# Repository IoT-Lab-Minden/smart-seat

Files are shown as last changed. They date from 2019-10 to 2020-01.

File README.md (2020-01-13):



# SmartSeat

SmartSeat is an office chair that automatically detects and adjusts to the user's favorite seat settings.

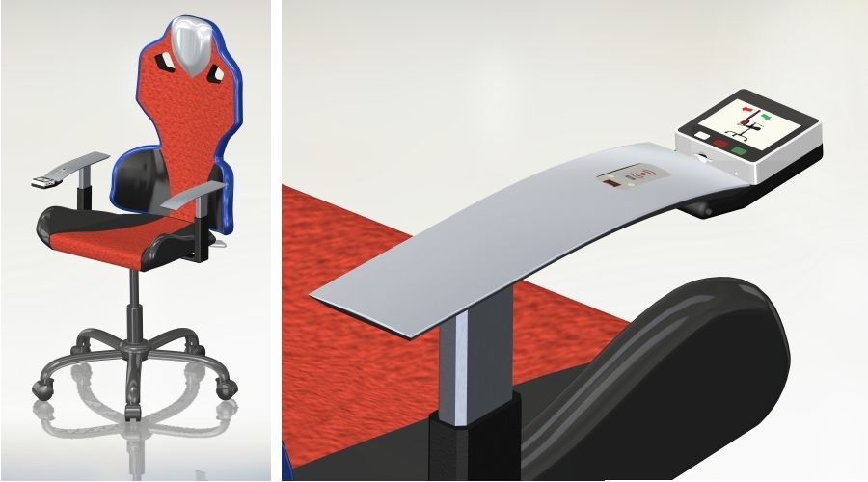
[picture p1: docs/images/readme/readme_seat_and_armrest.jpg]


## For documentation head over to the
## [SmartSeat-Wiki](https://github.com/IoT-Lab-Minden/smart-seat/wiki)

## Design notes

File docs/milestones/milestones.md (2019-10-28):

### 28.10.19: Rohkonstruktion / vorläufige Stückliste

### 04.11.19: jeweils eine Servo Baugruppe mechanisch fertig

### 11.11.19: Servo Baugruppe funktionsfähig

### 18.11.19: RFID lese und schreibfähig

### 09.12.19: Teile gedruckt

### 16.12.19: Aufbau komplett

### 13.01.20: Projektabgabe

### 20.01.20: Projektvorstellung

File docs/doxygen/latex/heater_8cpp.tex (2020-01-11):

\hypertarget{heater_8cpp}{}\doxysection{main/src/heater.cpp File Reference}
\label{heater_8cpp}\index{main/src/heater.cpp@{main/src/heater.cpp}}

Source code for the \mbox{\hyperlink{class_heater}{Heater}} class.  

{\ttfamily \#include \char`\"{}../include/heater.\+hpp\char`\"{}}\newline

\doxysubsection{Detailed Description}
Source code for the \mbox{\hyperlink{class_heater}{Heater}} class. 

\begin{DoxyAuthor}{Author}
Torsten Niemeier 

E-\/mail\+: \href{mailto:tniemeier1@fh-bielefeld.de}{\texttt{ tniemeier1@fh-\/bielefeld.\+de}} 
\end{DoxyAuthor}
\begin{DoxyVersion}{Version}
1.\+0 
\end{DoxyVersion}
\begin{DoxyDate}{Date}
2019/12/21
\end{DoxyDate}
\hypertarget{statemachine_8cpp_LICENSE}{}\doxysubsection{L\+I\+C\+E\+N\+SE}\label{statemachine_8cpp_LICENSE}
This program is free software; you can redistribute it and/or modify it under the terms of the G\+NU General Public License as published by the Free Software Foundation; either version 2 of the License, or (at your option) any later version.

This program is distributed in the hope that it will be useful, but W\+I\+T\+H\+O\+UT A\+NY W\+A\+R\+R\+A\+N\+TY; without even the implied warranty of M\+E\+R\+C\+H\+A\+N\+T\+A\+B\+I\+L\+I\+TY or F\+I\+T\+N\+E\+SS F\+OR A P\+A\+R\+T\+I\+C\+U\+L\+AR P\+U\+R\+P\+O\+SE. See the G\+NU General Public License for more details at \href{https://www.gnu.org/copyleft/gpl.html}{\texttt{ https\+://www.\+gnu.\+org/copyleft/gpl.\+html}}\hypertarget{statemachine_8cpp_DESCRIPTION}{}\doxysubsection{D\+E\+S\+C\+R\+I\+P\+T\+I\+ON}\label{statemachine_8cpp_DESCRIPTION}
The \mbox{\hyperlink{class_heater}{Heater}} class represents a physically present heating element.

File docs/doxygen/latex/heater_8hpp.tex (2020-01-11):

\hypertarget{heater_8hpp}{}\doxysection{main/include/heater.hpp File Reference}
\label{heater_8hpp}\index{main/include/heater.hpp@{main/include/heater.hpp}}

Header for the \mbox{\hyperlink{class_heater}{Heater}} class.  

{\ttfamily \#include $<$Arduino.\+h$>$}\newline
{\ttfamily \#include \char`\"{}../lib/\+M5\+Stack\+\_\+new.\+h\char`\"{}}\newline
{\ttfamily \#include \char`\"{}speeder.\+hpp\char`\"{}}\newline
\doxysubsection*{Classes}
\begin{DoxyCompactItemize}
\item 
class \mbox{\hyperlink{class_heater}{Heater}}
\end{DoxyCompactItemize}

\doxysubsection{Detailed Description}
Header for the \mbox{\hyperlink{class_heater}{Heater}} class. 

\begin{DoxyAuthor}{Author}
Torsten Niemeier 

E-\/mail\+: \href{mailto:tniemeier1@fh-bielefeld.de}{\texttt{ tniemeier1@fh-\/bielefeld.\+de}} 
\end{DoxyAuthor}
\begin{DoxyVersion}{Version}
1.\+0 
\end{DoxyVersion}
\begin{DoxyDate}{Date}
2019/12/30
\end{DoxyDate}
\hypertarget{statemachine_8cpp_LICENSE}{}\doxysubsection{L\+I\+C\+E\+N\+SE}\label{statemachine_8cpp_LICENSE}
This program is free software; you can redistribute it and/or modify it under the terms of the G\+NU General Public License as published by the Free Software Foundation; either version 2 of the License, or (at your option) any later version.

This program is distributed in the hope that it will be useful, but W\+I\+T\+H\+O\+UT A\+NY W\+A\+R\+R\+A\+N\+TY; without even the implied warranty of M\+E\+R\+C\+H\+A\+N\+T\+A\+B\+I\+L\+I\+TY or F\+I\+T\+N\+E\+SS F\+OR A P\+A\+R\+T\+I\+C\+U\+L\+AR P\+U\+R\+P\+O\+SE. See the G\+NU General Public License for more details at \href{https://www.gnu.org/copyleft/gpl.html}{\texttt{ https\+://www.\+gnu.\+org/copyleft/gpl.\+html}}\hypertarget{statemachine_8cpp_DESCRIPTION}{}\doxysubsection{D\+E\+S\+C\+R\+I\+P\+T\+I\+ON}\label{statemachine_8cpp_DESCRIPTION}
The \mbox{\hyperlink{class_heater}{Heater}} class represents a physically present heating element.

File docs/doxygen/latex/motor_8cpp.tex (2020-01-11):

\hypertarget{motor_8cpp}{}\doxysection{main/src/motor.cpp File Reference}
\label{motor_8cpp}\index{main/src/motor.cpp@{main/src/motor.cpp}}

Source code for the \mbox{\hyperlink{class_motor}{Motor}} class.  

{\ttfamily \#include \char`\"{}../include/motor.\+hpp\char`\"{}}\newline

\doxysubsection{Detailed Description}
Source code for the \mbox{\hyperlink{class_motor}{Motor}} class. 

\begin{DoxyAuthor}{Author}
Torsten Niemeier 

E-\/mail\+: \href{mailto:tniemeier1@fh-bielefeld.de}{\texttt{ tniemeier1@fh-\/bielefeld.\+de}} 
\end{DoxyAuthor}
\begin{DoxyVersion}{Version}
1.\+0 
\end{DoxyVersion}
\begin{DoxyDate}{Date}
2019/12/21
\end{DoxyDate}
\hypertarget{statemachine_8cpp_LICENSE}{}\doxysubsection{L\+I\+C\+E\+N\+SE}\label{statemachine_8cpp_LICENSE}
This program is free software; you can redistribute it and/or modify it under the terms of the G\+NU General Public License as published by the Free Software Foundation; either version 2 of the License, or (at your option) any later version.

This program is distributed in the hope that it will be useful, but W\+I\+T\+H\+O\+UT A\+NY W\+A\+R\+R\+A\+N\+TY; without even the implied warranty of M\+E\+R\+C\+H\+A\+N\+T\+A\+B\+I\+L\+I\+TY or F\+I\+T\+N\+E\+SS F\+OR A P\+A\+R\+T\+I\+C\+U\+L\+AR P\+U\+R\+P\+O\+SE. See the G\+NU General Public License for more details at \href{https://www.gnu.org/copyleft/gpl.html}{\texttt{ https\+://www.\+gnu.\+org/copyleft/gpl.\+html}}\hypertarget{statemachine_8cpp_DESCRIPTION}{}\doxysubsection{D\+E\+S\+C\+R\+I\+P\+T\+I\+ON}\label{statemachine_8cpp_DESCRIPTION}
The \mbox{\hyperlink{class_motor}{Motor}} class represents a physically present dc-\/motor.

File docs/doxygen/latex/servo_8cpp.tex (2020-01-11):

\hypertarget{servo_8cpp}{}\doxysection{main/src/servo.cpp File Reference}
\label{servo_8cpp}\index{main/src/servo.cpp@{main/src/servo.cpp}}

Source code for the \mbox{\hyperlink{class_servo}{Servo}} class.  

{\ttfamily \#include \char`\"{}../include/servo.\+hpp\char`\"{}}\newline

\doxysubsection{Detailed Description}
Source code for the \mbox{\hyperlink{class_servo}{Servo}} class. 

\begin{DoxyAuthor}{Author}
Torsten Niemeier 

E-\/mail\+: \href{mailto:tniemeier1@fh-bielefeld.de}{\texttt{ tniemeier1@fh-\/bielefeld.\+de}} 
\end{DoxyAuthor}
\begin{DoxyVersion}{Version}
1.\+0 
\end{DoxyVersion}
\begin{DoxyDate}{Date}
2019/12/21
\end{DoxyDate}
\hypertarget{statemachine_8cpp_LICENSE}{}\doxysubsection{L\+I\+C\+E\+N\+SE}\label{statemachine_8cpp_LICENSE}
This program is free software; you can redistribute it and/or modify it under the terms of the G\+NU General Public License as published by the Free Software Foundation; either version 2 of the License, or (at your option) any later version.

This program is distributed in the hope that it will be useful, but W\+I\+T\+H\+O\+UT A\+NY W\+A\+R\+R\+A\+N\+TY; without even the implied warranty of M\+E\+R\+C\+H\+A\+N\+T\+A\+B\+I\+L\+I\+TY or F\+I\+T\+N\+E\+SS F\+OR A P\+A\+R\+T\+I\+C\+U\+L\+AR P\+U\+R\+P\+O\+SE. See the G\+NU General Public License for more details at \href{https://www.gnu.org/copyleft/gpl.html}{\texttt{ https\+://www.\+gnu.\+org/copyleft/gpl.\+html}}\hypertarget{statemachine_8cpp_DESCRIPTION}{}\doxysubsection{D\+E\+S\+C\+R\+I\+P\+T\+I\+ON}\label{statemachine_8cpp_DESCRIPTION}
The \mbox{\hyperlink{class_servo}{Servo}} class represents a combination of one motor and one potentiometer.

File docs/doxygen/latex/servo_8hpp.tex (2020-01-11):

\hypertarget{servo_8hpp}{}\doxysection{main/include/servo.hpp File Reference}
\label{servo_8hpp}\index{main/include/servo.hpp@{main/include/servo.hpp}}

Header for the \mbox{\hyperlink{class_servo}{Servo}} class.  

{\ttfamily \#include \char`\"{}motor.\+hpp\char`\"{}}\newline
{\ttfamily \#include \char`\"{}potentiometer.\+hpp\char`\"{}}\newline
{\ttfamily \#include \char`\"{}../include/config.\+hpp\char`\"{}}\newline
\doxysubsection*{Classes}
\begin{DoxyCompactItemize}
\item 
class \mbox{\hyperlink{class_servo}{Servo}}
\end{DoxyCompactItemize}

\doxysubsection{Detailed Description}
Header for the \mbox{\hyperlink{class_servo}{Servo}} class. 

\begin{DoxyAuthor}{Author}
Torsten Niemeier 

E-\/mail\+: \href{mailto:tniemeier1@fh-bielefeld.de}{\texttt{ tniemeier1@fh-\/bielefeld.\+de}} 
\end{DoxyAuthor}
\begin{DoxyVersion}{Version}
1.\+0 
\end{DoxyVersion}
\begin{DoxyDate}{Date}
2019/12/30
\end{DoxyDate}
\hypertarget{statemachine_8cpp_LICENSE}{}\doxysubsection{L\+I\+C\+E\+N\+SE}\label{statemachine_8cpp_LICENSE}
This program is free software; you can redistribute it and/or modify it under the terms of the G\+NU General Public License as published by the Free Software Foundation; either version 2 of the License, or (at your option) any later version.

This program is distributed in the hope that it will be useful, but W\+I\+T\+H\+O\+UT A\+NY W\+A\+R\+R\+A\+N\+TY; without even the implied warranty of M\+E\+R\+C\+H\+A\+N\+T\+A\+B\+I\+L\+I\+TY or F\+I\+T\+N\+E\+SS F\+OR A P\+A\+R\+T\+I\+C\+U\+L\+AR P\+U\+R\+P\+O\+SE. See the G\+NU General Public License for more details at \href{https://www.gnu.org/copyleft/gpl.html}{\texttt{ https\+://www.\+gnu.\+org/copyleft/gpl.\+html}}\hypertarget{statemachine_8cpp_DESCRIPTION}{}\doxysubsection{D\+E\+S\+C\+R\+I\+P\+T\+I\+ON}\label{statemachine_8cpp_DESCRIPTION}
The \mbox{\hyperlink{class_servo}{Servo}} class represents a physically present servo device, a combination of one dc-\/motor and one potentiometer.

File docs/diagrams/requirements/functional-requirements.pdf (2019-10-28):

Note..
Due to sensor/device
decisions the storage of data will only be able if the user's ID-Chip is near (about 8cm) to the RFID-Reader/Writer

Note..
The prototype will not contain a battery because of size
restrictions.
It will be powered
by a power adapter.
(6V or higher)

«requirement»
User Warning
-id = "R4.1.2."
-text = "The system shall be able to warn the user if the battery needs to be charged."

«requirement»
Battery Capacity
-id = "R4.1.1."
-text = "The system's battery capacity shall be able to supply the system with electric power at least 2 days without charging."

«requirement»
Power Supply
-id = "R4.1."
-text = "The system shall contain a battery to provide electric power."

«requirement»
Mobility
-id = "R4."
-text = "The system shall be able to operate without being connected to a stationary power supply."

«requirement»
Position Measurements
-id = "R2.3.1.7."
-text = "The system shall be able to detect the current positions
of the adjustable seat elements immediately at any time to control the motors."

«requirement»
Device Decision
-id = "D2.1."
-text = "The system shall use a RFID-Reader/Writer to store the changed user's data on a
RFID-Chip."

«requirement»
Adjustment Function Display -id = "R3.2.1.4."
-text = "The system shall contain
a device to show the adjustment function selected by the user."

«requirement»
Actuator Decision
-id = "D3.4."
-text = "The system shall use the display of the M5Stack to show the user which function is currently selected."

«requirement»
Decrease Choice
-id = "R3.2.1.3."
-text = "The system shall contain a pushbutton to decrease the selected seat adjustment value."

«requirement»
Sensor Decision
-id = "D3.3."
-text = "The system shall use the middle pushbutton of the M5Stack to increase the adjustment value."

«requirement»
Increase Choice
-id = "R3.2.1.2."
-text = "The system shall contain a pushbutton to increase the selected seat adjustment value."

«requirement»
Sensor Decision
-id = "D3.2."
-text = "The system shall use the right pushbutton of the M5Stack to increase the adjustment value."

«requirement»
Function Selection
-id = "R3.2.1.1."
-text = "The system shall contain a pushbutton to select the seat adjustment that shall be changed."

«requirement»
Sensor Decision
-id = "D3.1."
-text = "The system shall use the left pushbutton of the M5Stack to select the adjustment function."

«block»
M5Stack
-with Display
-with 3 Buttons

«requirement»
Input Device
-id = "R3.2.1."
-text = "The system shall contain an input device with at least three pushbuttons."

«requirement»
Acceptance of commands
-id = "R3.2."
-text = "The system shall be able to receive manual commands by the user."

«requirement»
Armrest Height Detection
-id = "R2.3.1.7.6."
-text = "The system shall be able to measure the current height of the armrests immediately without the need to approach a reference point."

«requirement»
Backrest Offset Detection
-id = "R2.3.1.7.5."
-text = "The system shall be able to measure the current offset of the backrest immediately without the need to approach a reference point."

«requirement»
Backrest Angle Detection
-id = "R2.3.1.7.4."
-text = "The system shall be able to measure the current angle of the backrest immediately without the need to approach a reference point."

«requirement»
Backrest Height Detection
-id = "R2.3.1.7.3."
-text = "The system shall be able to measure the current height of the backrest immediately without the need to approach a reference point."

«requirement»
Seat Angle Detection
-id = "R2.3.1.7.2."
-text = "The system shall be able to measure the current seat angle immediately without the need to approach a reference point."

«requirement»
Seat Height Detection
-id = "R2.3.1.7.1."
-text = "The system shall be able to measure the current seat height immediately without the need to approach a reference point."

«block»
Rotary
Potentiometer

«requirement»
Sensor Decision
-id = "D2.15."
-text = "The system shall use an absolute angle encoder to detect the height of the armrests."

«requirement»
Sensor Decision
-id = "D2.11."
-text = "The system shall use an absolute angle encoder to detect the angle of the seat."

«block»
Rotary
Potentiometer

«block»
Gearmotor
with
Crank Drive

«requirement»
Actuator Decision
-id = "D2.9."
-text = "The system shall use a electric gearmotor to adjust the height of the armrests."

«requirement»
Motorized Armrest Height Adjustment -id = "R2.3.1.6."
-text = "The system shall be able to adjust the height of the armrests motorized."

«requirement»
Motorized Backrest Height Adjustment -id = "R2.3.1.3."
-text = "The system shall be able to adjust the height of the backrest motorized."

«requirement»
Actuator Decision
-id = "D2.6."
-text = "The system shall use a electric gearmotor to adjust the height of the backrest."

«block»
Gearmotor
with
Screw Drive

«block»
Gearmotor
with
Crank Drive

«requirement»
Actuator Decision
-id = "D2.7."
-text = "The system shall use a electric gearmotor to adjust the angle of the backrest."

«requirement»
Motorized Backrest Angle Adjustment -id = "R2.3.1.4."
-text = "The system shall be able to adjust the angle of the backrest motorized."

«block»
Gearmotor
with
Screw Drive

«requirement»
Actuator Decision
-id = "D2.8."
-text = "The system shall use a electric gearmotor to adjust the offset of the backrest."

«requirement»
Motorized Backrest Offset Adjustment -id = "R2.3.1.5."
-text = "The system shall be able to adjust the offset of the backrest motorized."

«block»
Gearmotor
with
Crank Drive

«requirement»
Actuator Decision
-id = "D2.5."
-text = "The system shall use a electric gearmotor to adjust the angle of the seat."

«requirement»
Motorized Seat Angle Adjustment -id = "R2.3.1.2."
-text = "The system shall be able to adjust the angle of the seat motorized."

«requirement»
Motorized Seat Height Adjustment -id = "R2.3.1.1."
-text = "The system shall be able to adjust the height of the seat motorized."

«requirement»
Actuator Decision
-id = "D2.4."
-text = "The system shall use a electric gearmotor to adjust the height of the seat."

«block»
Gearmotor
with
Crank Drive

«requirement»
Manual Adjustments
-id = "R3.1."
-text = "The system shall be able to adjust all adjustable elements of the chair according to the user's commands."

«requirement»
Data Accessibility
-id = "R2.1.1."
-text = "The user's data shall be accessible to the system at the moment the user approaches the system."

«requirement»
Data Location
-id = "R2.1.1.1."
-text = "The System shall store the user's data at the user's body."

«block»
RFID-Chip

«requirement»
Data Storage Device
-id = "R2.1.2.1."
-text = "The storage device for
the user's data shall be capable
to store at least 6 integer numbers."

«requirement»
User Data
-id = "R2.1.2."
-text = "The user's preferred seat adjustment data shall be stored on a suitable device."

«block»
Linear
Potentiometer

«requirement»
Sensor Decision
-id = "D2.14."
-text = "The system shall use an absolute distance measuring system to detect the offset of the backrest."

«block»
Linear
Potentiometer

«requirement»
Sensor Decision
-id = "D2.12."
-text = "The system shall use an absolute distance measuring system to detect the height of the backrest."

«requirement»
Motorized Adjustments
-id = "R2.3.1."
-text = "The system shall be able to adjust all adjustable elements motorized."

«requirement»
Sensor Decision
-id = "D2.10."
-text = "The system shall use an absolute distance measuring system to detect the height of the seat."

«requirement»
Sensor Decision
-id = "D2.13."
-text = "The system shall use an absolute angle encoder to detect the angle of the backrest."

«block»
Linear
Potentiometer

«block»
Rotary
Potentiometer

«block»
RFID-Sensor
Reader/Writer

«requirement»
Devise Decision
-id = "D2.2."
-text = "The system shall use a RFID-Chip to store user's data."

«requirement»
Sensor Decision
-id = "D2.3."
-text = "The system shall use a RFID-Sensor to recognize a user."

«requirement»
Automatic Adjustments
-id = "R2.3."
-text = "The system shall be able to adjust all adjustable elements of the chair according to the user's data."

«requirement»
Data Determination
-id = "R2.1."
-text = "The system shall be able to determine the user's preferred chair adjustment data."

«requirement»
User Recognition
-id = "R2.2."
-text = "The system shall be capable to recognize a user
as he/she approaches the system."

«requirement»
Data Storage
-id = "R1."
-text = "The system shall be able to save the current settings set manually by the user, so that they can be assigned to the specific user."

«requirement»
Manual Adjustments
-id = "R3."
-text = "The system shall be able to receive
manual commands by the user and adjust the chair settings according to the given commands."

«requirement»
SmartSeat

«requirement»
User Adaption
-id = "R2."
-text = "The system shall be capable to recognize
a user as he/she approaches the system, detect the user's preferred chair adjustment data and adjust all adjustable elements of the seat according to the read out data."

req [package] Functional Requirements [functional requirements diagram]

«deriveReqt»

«satisfy»

«refine»

«deriveReqt»

«refine»

«deriveReqt»

«refine»

«satisfy»

«satisfy»

«deriveReqt»

«deriveReqt»

«refine»

«refine» | «satisfy»

«satisfy»
«refine»

«satisfy»

«refine»

«refine» | «satisfy»

«deriveReqt»

«refine»

«refine»

«refine»

«refine»

«refine»

«refine»

«satisfy»

«satisfy»

«deriveReqt»

«deriveReqt»

«refine» | «satisfy»
«refine» | «satisfy»
«refine» | «satisfy»
«refine» | «satisfy»
«refine» | «satisfy»
«refine» | «satisfy»

«deriveReqt»

«deriveReqt»

«deriveReqt» | «deriveReqt»

«deriveReqt»

«satisfy»

«deriveReqt»

«satisfy»

«deriveReqt»

«satisfy»

«satisfy»

«satisfy»

«satisfy»

«satisfy»

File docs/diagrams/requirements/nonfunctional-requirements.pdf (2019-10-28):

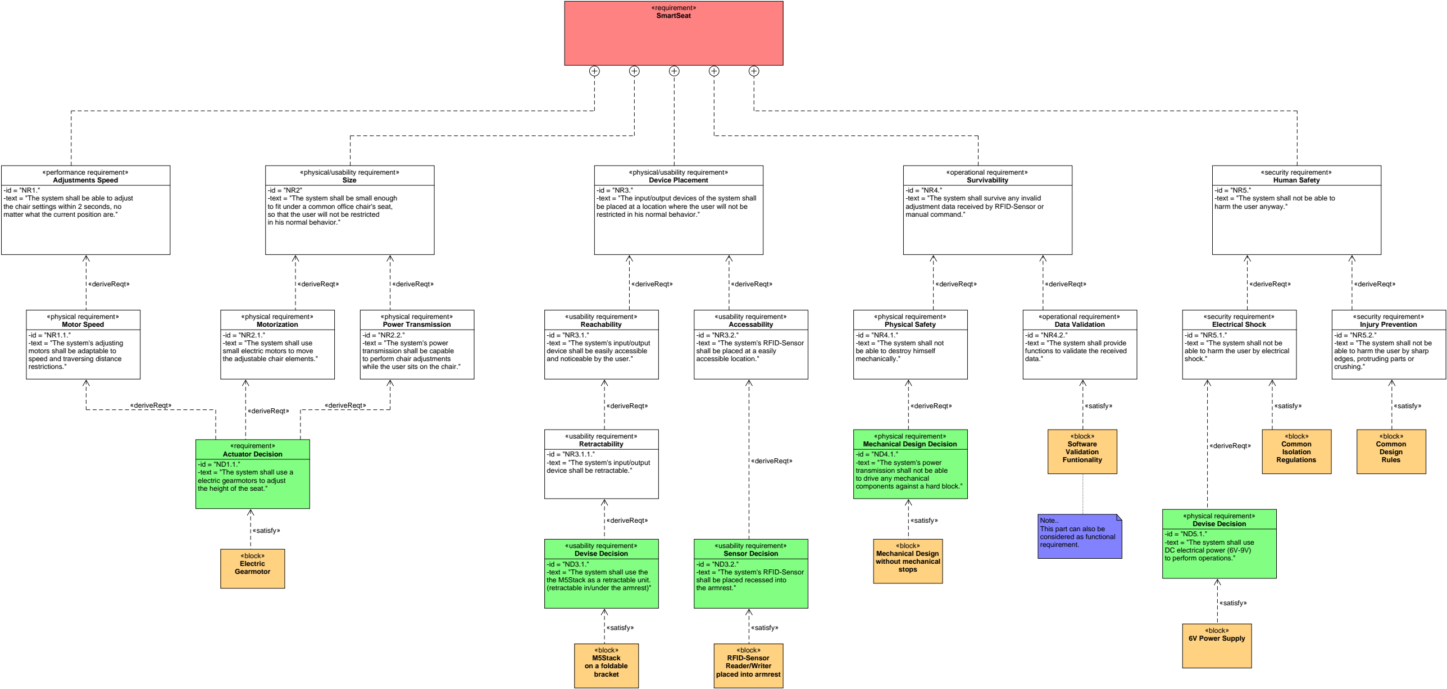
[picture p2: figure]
«block» Common Design Rules; «security requirement» Injury Prevention -id = "NR5.2." -text = "The system shall not be able to harm the user by sharp edges, protruding parts or crushing."; «physical requirement» Devise Decision -id = "ND5.1." -text = "The system shall use DC electrical power (6V-9V) to perform operations."; «block» Common Isolation Regulations; «block» 6V Power Supply; «security requirement» Electrical Shock -id = "NR5.1." -text = "The system shall not be able to harm the user by electrical shock."; «security requirement» Human Safety; harm the user anyway."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

-text = "The system shall not be able to

-text = "The system shall survive any invalid adjustment data received by RFID-Sensor or

-text = "The system shall be small enough to fit under a common office chair's seat,

-text = "The system shall be able to adjust

-text = "The input/output devices of the system shall be placed at a location where the user will not be req [package] Nonfunctional Requirements [nonfunctional requirements diagram]

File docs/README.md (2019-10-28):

## Welcome

SmartSeat is an office chair that automatically adjusts to the user's preferred seat parameters.



The controlled parameters are:
- the height of the seat
- the angle of the seat
- the height of the backrest
- the angle of the backrest
- the offset of the backrest
- the height of the armrests

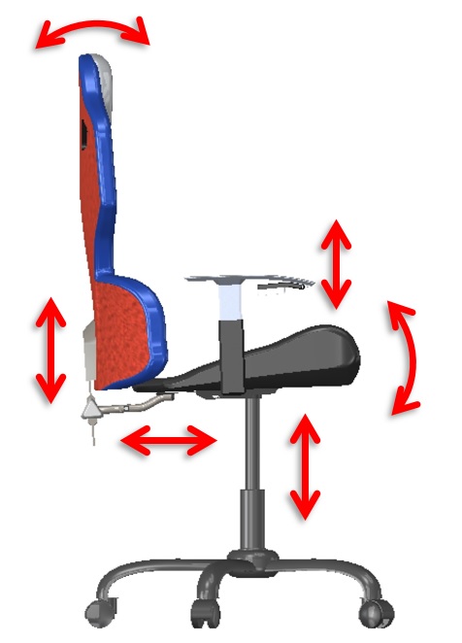
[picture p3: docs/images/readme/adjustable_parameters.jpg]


The user will be recognized by a RFID-chip that can be worn as a bracelet, a keychain or just as RFID-card.
The user's seat parameters will be stored on the RFID-chip and, once read out by the chair's sensor, the chair will adjust himself due to the received data.

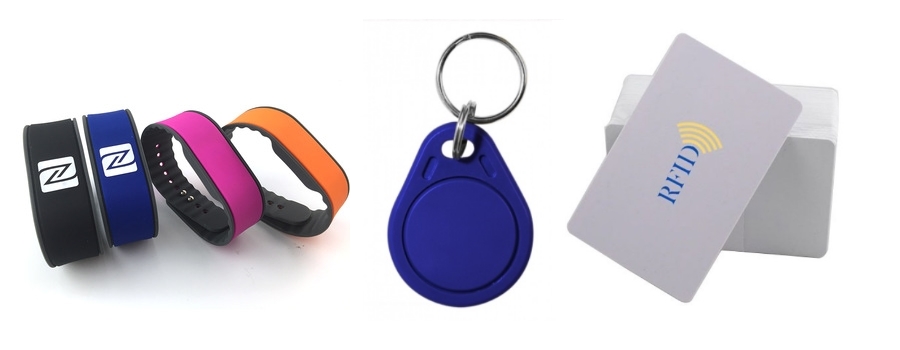
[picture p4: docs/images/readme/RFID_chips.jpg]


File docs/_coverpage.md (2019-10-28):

# SmartSeat
### ... the self-adjusting office chair ...
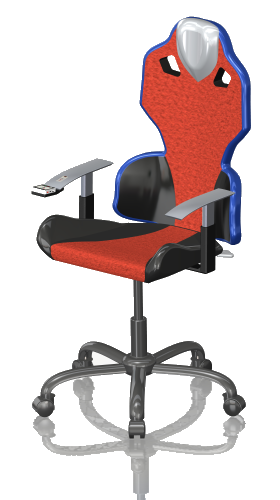
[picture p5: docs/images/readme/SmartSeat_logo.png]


[Overview](#main)
[Used Hardware](https://iot-lab-minden.github.io/SmartSeat/#/?id=used-hardware)
[GitHub](https://github.com/IoT-Lab-Minden/SmartSeat)

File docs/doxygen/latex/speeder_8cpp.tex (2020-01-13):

\hypertarget{speeder_8cpp}{}\doxysection{main/src/speeder.cpp File Reference}
\label{speeder_8cpp}\index{main/src/speeder.cpp@{main/src/speeder.cpp}}

Source code for the \mbox{\hyperlink{class_speeder}{Speeder}} class.  

{\ttfamily \#include \char`\"{}../include/speeder.\+hpp\char`\"{}}\newline

\doxysubsection{Detailed Description}
Source code for the \mbox{\hyperlink{class_speeder}{Speeder}} class. 

\begin{DoxyAuthor}{Author}
Torsten Niemeier 

E-\/mail\+: \href{mailto:tniemeier1@fh-bielefeld.de}{\texttt{ tniemeier1@fh-\/bielefeld.\+de}} 
\end{DoxyAuthor}
\begin{DoxyVersion}{Version}
1.\+0 
\end{DoxyVersion}
\begin{DoxyDate}{Date}
2019/12/21
\end{DoxyDate}
\hypertarget{statemachine_8cpp_LICENSE}{}\doxysubsection{L\+I\+C\+E\+N\+SE}\label{statemachine_8cpp_LICENSE}
This program is free software; you can redistribute it and/or modify it under the terms of the G\+NU General Public License as published by the Free Software Foundation; either version 2 of the License, or (at your option) any later version.

This program is distributed in the hope that it will be useful, but W\+I\+T\+H\+O\+UT A\+NY W\+A\+R\+R\+A\+N\+TY; without even the implied warranty of M\+E\+R\+C\+H\+A\+N\+T\+A\+B\+I\+L\+I\+TY or F\+I\+T\+N\+E\+SS F\+OR A P\+A\+R\+T\+I\+C\+U\+L\+AR P\+U\+R\+P\+O\+SE. See the G\+NU General Public License for more details at \href{https://www.gnu.org/copyleft/gpl.html}{\texttt{ https\+://www.\+gnu.\+org/copyleft/gpl.\+html}}\hypertarget{statemachine_8cpp_DESCRIPTION}{}\doxysubsection{D\+E\+S\+C\+R\+I\+P\+T\+I\+ON}\label{statemachine_8cpp_DESCRIPTION}
The \mbox{\hyperlink{class_speeder}{Speeder}} class represents a microcontroller\textquotesingle{}s pwm output to drive a dc-\/motor.

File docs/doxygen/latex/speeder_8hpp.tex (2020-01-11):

\hypertarget{speeder_8hpp}{}\doxysection{main/include/speeder.hpp File Reference}
\label{speeder_8hpp}\index{main/include/speeder.hpp@{main/include/speeder.hpp}}

Header for the \mbox{\hyperlink{class_speeder}{Speeder}} class.  

{\ttfamily \#include $<$Arduino.\+h$>$}\newline
{\ttfamily \#include \char`\"{}../lib/\+M5\+Stack\+\_\+new.\+h\char`\"{}}\newline
\doxysubsection*{Classes}
\begin{DoxyCompactItemize}
\item 
class \mbox{\hyperlink{class_speeder}{Speeder}}
\end{DoxyCompactItemize}

\doxysubsection{Detailed Description}
Header for the \mbox{\hyperlink{class_speeder}{Speeder}} class. 

\begin{DoxyAuthor}{Author}
Torsten Niemeier 

E-\/mail\+: \href{mailto:tniemeier1@fh-bielefeld.de}{\texttt{ tniemeier1@fh-\/bielefeld.\+de}} 
\end{DoxyAuthor}
\begin{DoxyVersion}{Version}
1.\+0 
\end{DoxyVersion}
\begin{DoxyDate}{Date}
2019/12/30
\end{DoxyDate}
\hypertarget{statemachine_8cpp_LICENSE}{}\doxysubsection{L\+I\+C\+E\+N\+SE}\label{statemachine_8cpp_LICENSE}
This program is free software; you can redistribute it and/or modify it under the terms of the G\+NU General Public License as published by the Free Software Foundation; either version 2 of the License, or (at your option) any later version.

This program is distributed in the hope that it will be useful, but W\+I\+T\+H\+O\+UT A\+NY W\+A\+R\+R\+A\+N\+TY; without even the implied warranty of M\+E\+R\+C\+H\+A\+N\+T\+A\+B\+I\+L\+I\+TY or F\+I\+T\+N\+E\+SS F\+OR A P\+A\+R\+T\+I\+C\+U\+L\+AR P\+U\+R\+P\+O\+SE. See the G\+NU General Public License for more details at \href{https://www.gnu.org/copyleft/gpl.html}{\texttt{ https\+://www.\+gnu.\+org/copyleft/gpl.\+html}}\hypertarget{statemachine_8cpp_DESCRIPTION}{}\doxysubsection{D\+E\+S\+C\+R\+I\+P\+T\+I\+ON}\label{statemachine_8cpp_DESCRIPTION}
The \mbox{\hyperlink{class_speeder}{Speeder}} class represents a Microcontroller\textquotesingle{}s P\+W\+M-\/driven G\+P\+IO. It is used to control the speed or the power of the assigned device.

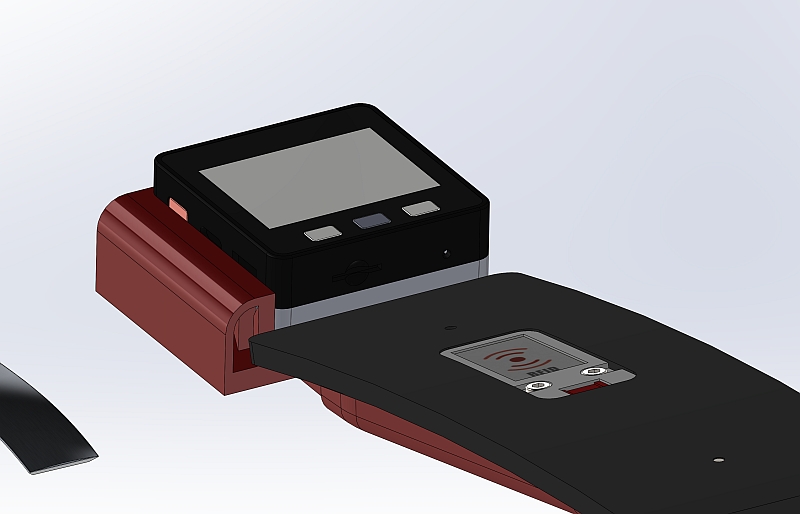
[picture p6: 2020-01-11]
docs/images/prototype/design/m5stack_02.jpg

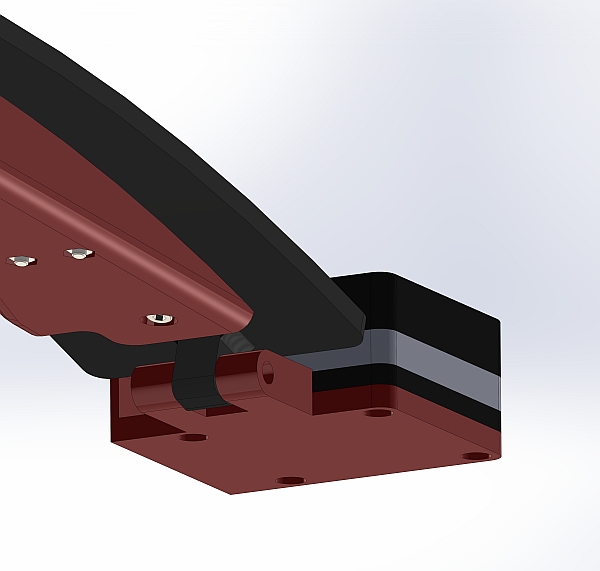
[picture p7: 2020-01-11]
docs/images/prototype/design/m5stack_01.jpg

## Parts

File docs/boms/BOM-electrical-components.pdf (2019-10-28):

### Bill of Materials

electrical components

No. | Quantity | Name | Description | Distributor | Pricing | Image
1 | 1 | M5STACK BASIC Controller | ESP32 Development Device | m5stack.com (https://m5stack.com/collections/m5-core/products/basic-core-iot-development-kit) | 27,95 $
| | | | Conrad (https://www.conrad.de/de/p/makerfactory-m5stack-basic-esp32-entwickler-kit-1888209.html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!!) | 39,99 €
2 | 2 | M5STACK DC-MOTOR Module | 4 Channels DC Encoder Motor driver module | m5stack.com (https://m5stack.com/collections/m5-module/products/lego-module) | 11,39 $
| | | | Conrad (https://www.conrad.de/de/p/makerfactory-m5stack-dc-motor-modul-2141872.html) | 15,99 €
3 | 1 | M5STACK Mini RFID Unit (MFRC522) | RFID-Transponder Reader/Writer | m5stack.com (https://m5stack.com/collections/m5-unit/products/rfid-sensor-unit) | 9,95 $
| | | | Conrad (https://www.conrad.de/de/p/makerfactory-m5stack-rfid-einheit-2108286.html) | 12,99 €
4 | 6 | M5STACK Mini Angle Unit with Potentiometer | 4 Channels DC Encoder Motor driver module | m5stack.com (https://m5stack.com/collections/m5-unit/products/angle-unit) | 1,99 $
| | | | Conrad (https://www.conrad.de/de/p/makerfactory-m5stack-potentiometer-2108270.html) | 2,99 €
5 | 3 | M5STACK 1 to 3 HUB Unit | m5stack.com (https://m5stack.com/collections/m5-unit/products/mini-hub-module) | 1,59 $
| | | Conrad (https://www.conrad.de/de/p/makerfactory-m5stack-grove-hub-2108273.html) | 2,99 €
m5stack.com (https://m5stack.com/collections/m5-accessory/products/13-56mhz-rfid-card-f08-chip-5pcs) | 2,00 $
7 | 6 | 6V DC Mini-Gearmotor 50 / 200 / 300 RPM | amazon (https://www.amazon.de/Yosoo-Drehmoment-Getriebemotor-Getriebe-Spielzeug/dp/B01BBSXDL2?adgrpid=69052659977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) | 8,79 €
| | | Pollin (https://www.pollin.de/p/gleichstrommotor-g50-mit-metallgetriebe-820218) | 9,90 €
8 | 1 | Universal PlugIn Power Supply 18W/24W | 3V/4,5V/5V/6V/7,5V/9V/12V | amazon (https://www.amazon.de/Universal-Switching-Selectable-Household-Electronics/dp/B07DB9K2C2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) | 16,59 €
| | | | Pollin (https://www.pollin.de/p/stecker-schaltnetzteil-logilink-pa0161-3-12-v-24-w-352288) | 11,95 €
6 | 1

M5STACK 13.56MHz RFID Card F08 Chip （5pcs）

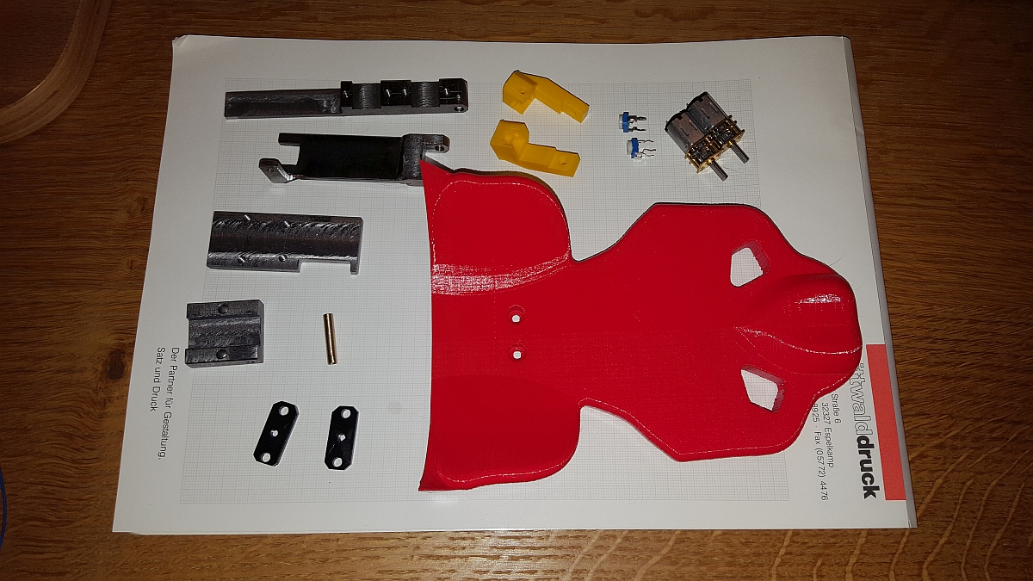
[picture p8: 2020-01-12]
docs/images/prototype/construction/resized/parts_01.jpg

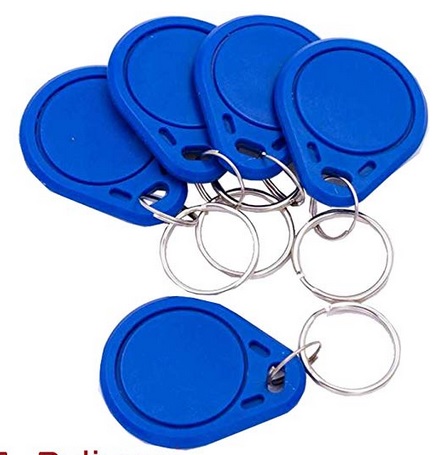
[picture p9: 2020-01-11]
docs/boms/images/rfidtag.jpg

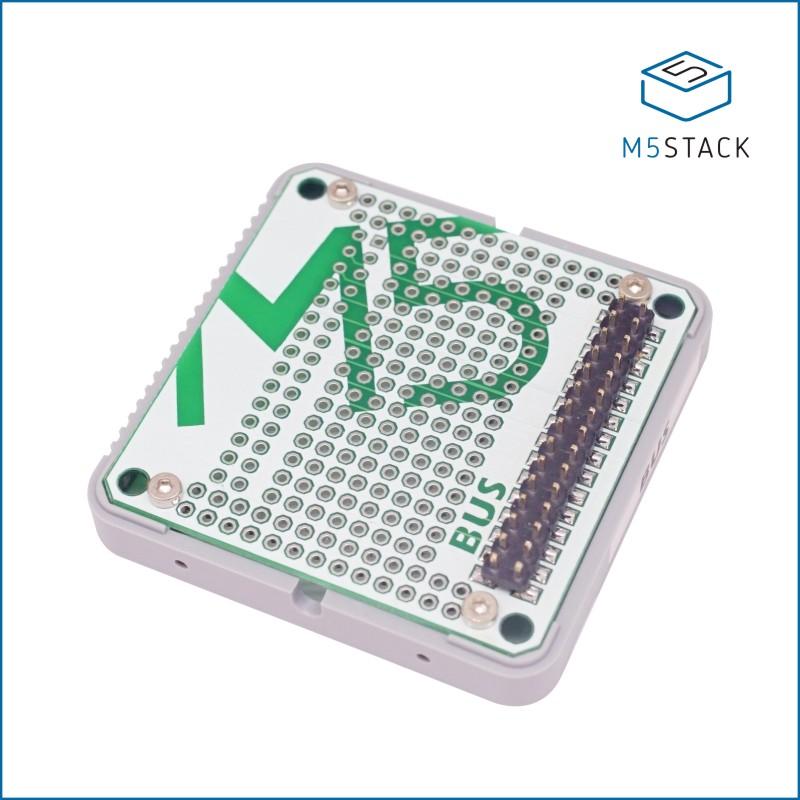
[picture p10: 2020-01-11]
docs/boms/images/BUS_1200x1200.jpg

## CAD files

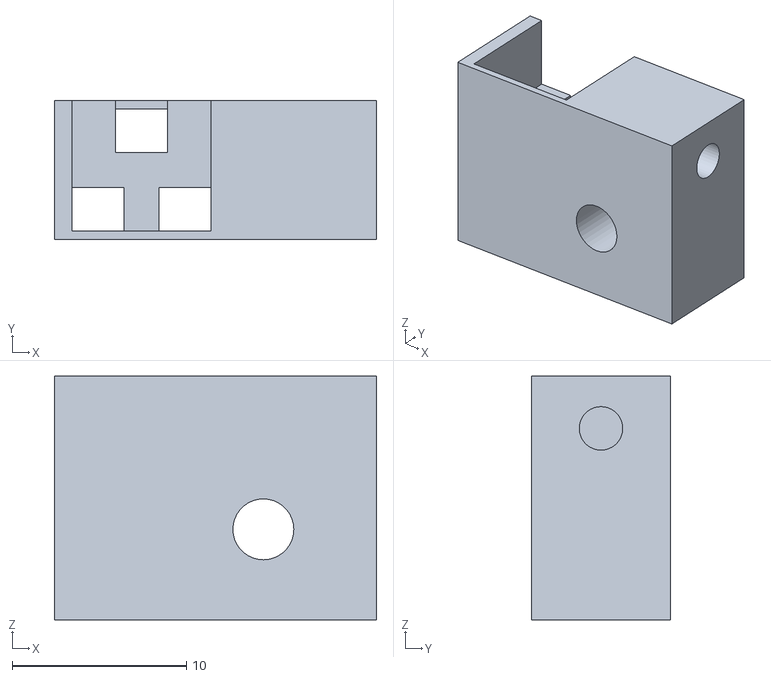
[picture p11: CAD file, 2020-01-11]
docs/images/prototype/mechanics/stl-files/00000021-Sensorhalter.STL
18.5 x 8.00 x 14.0

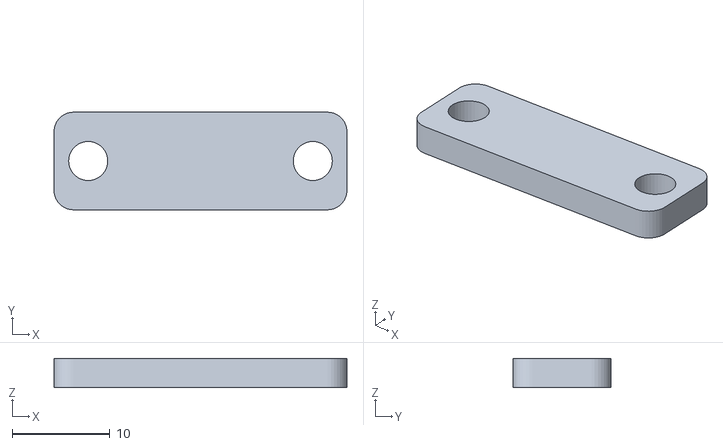
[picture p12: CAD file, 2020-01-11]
docs/images/prototype/mechanics/stl-files/00000028-Klemmstück.STL
30.0 x 10.0 x 3.00

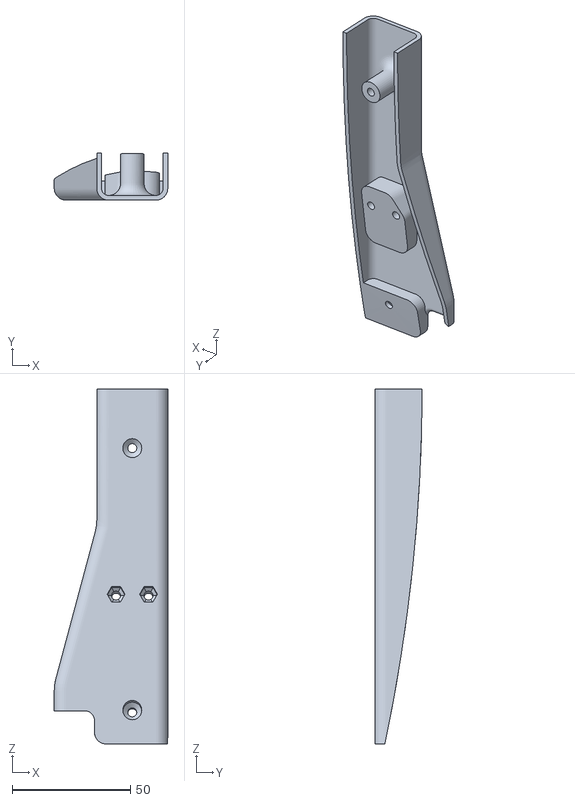
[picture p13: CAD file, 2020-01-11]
docs/images/prototype/mechanics/stl-files/00000050-Kabelkanal.STL
48.0 x 20.0 x 150.0

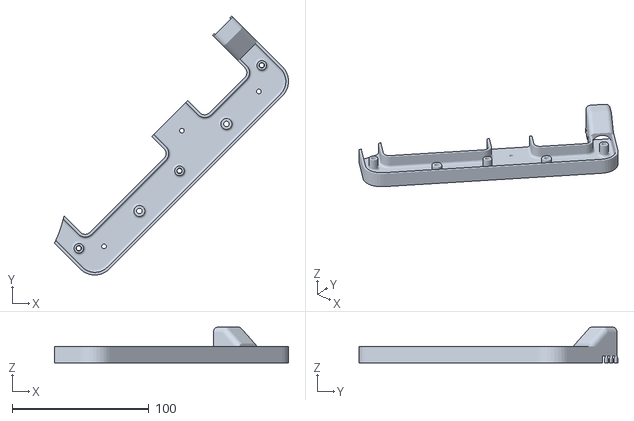
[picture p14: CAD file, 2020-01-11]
docs/images/prototype/mechanics/stl-files/00000052-Kabelkanal.STL
171.0 x 189.2 x 26.0

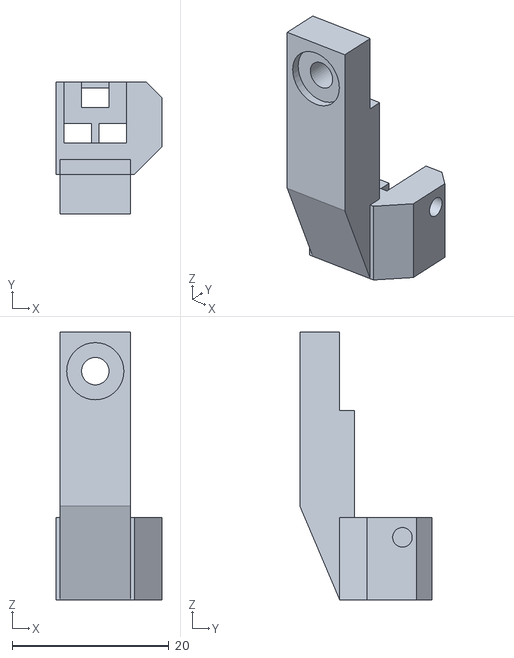
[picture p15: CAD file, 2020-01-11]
docs/images/prototype/mechanics/stl-files/00000044-Sensorhalter.STL
13.5 x 16.9 x 34.2

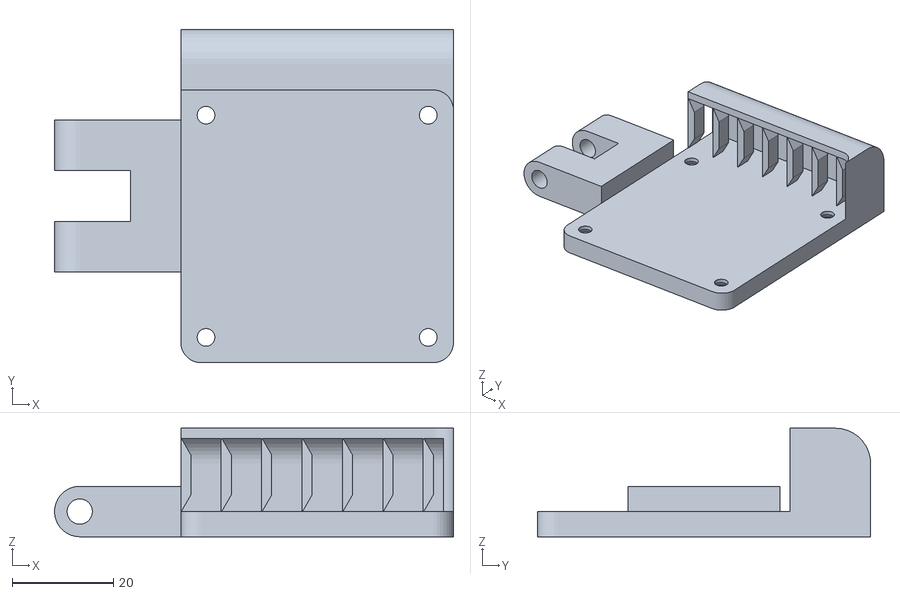
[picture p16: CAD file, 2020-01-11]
docs/images/prototype/mechanics/stl-files/00000034-Stackhalter.STL
79.0 x 66.0 x 21.5

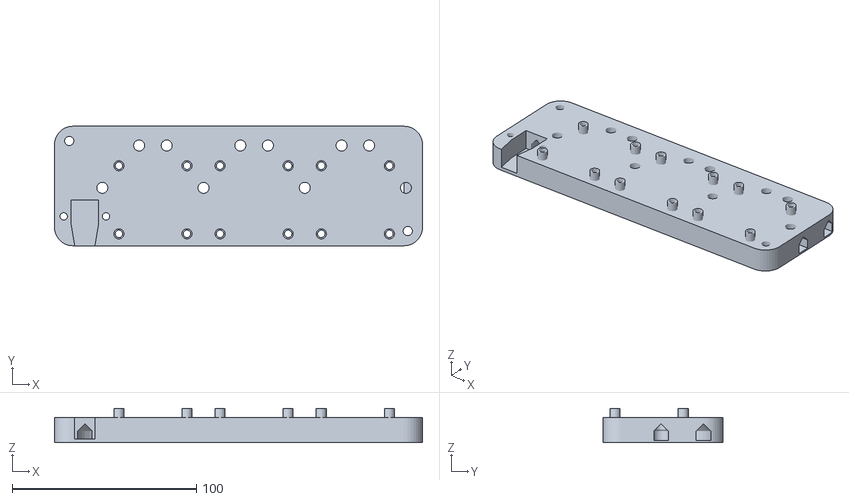
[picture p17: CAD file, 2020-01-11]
docs/images/prototype/mechanics/stl-files/00000027-Brückenhalter.STL
200.0 x 65.0 x 18.5

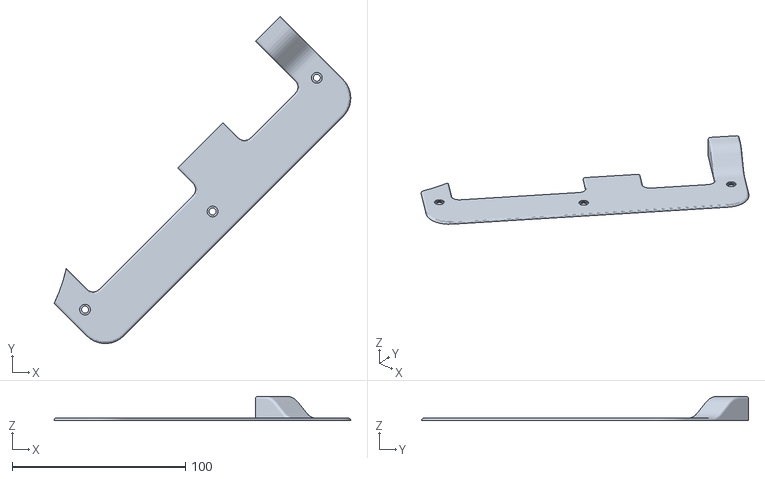
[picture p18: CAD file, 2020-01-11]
docs/images/prototype/mechanics/stl-files/00000055-Deckel.STL
171.0 x 188.5 x 14.0

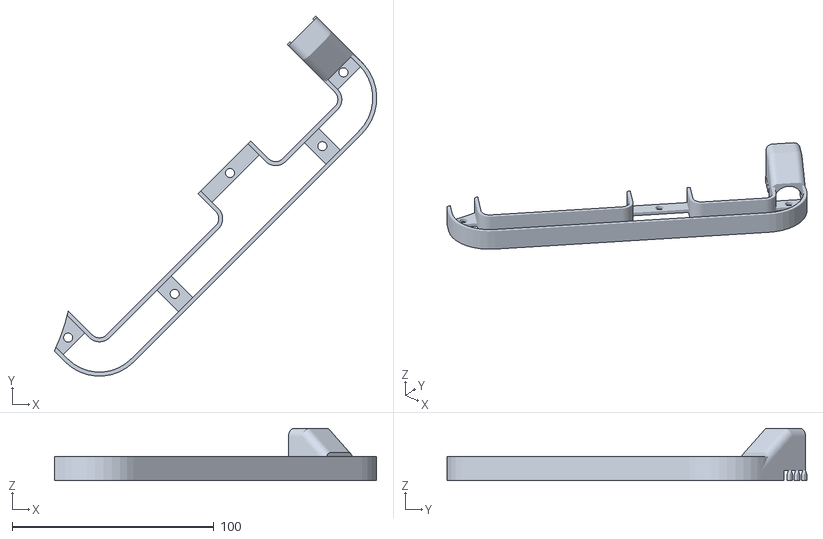
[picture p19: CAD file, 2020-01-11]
docs/images/prototype/mechanics/stl-files/00000051-Kabelkanal.STL
159.8 x 178.4 x 26.0

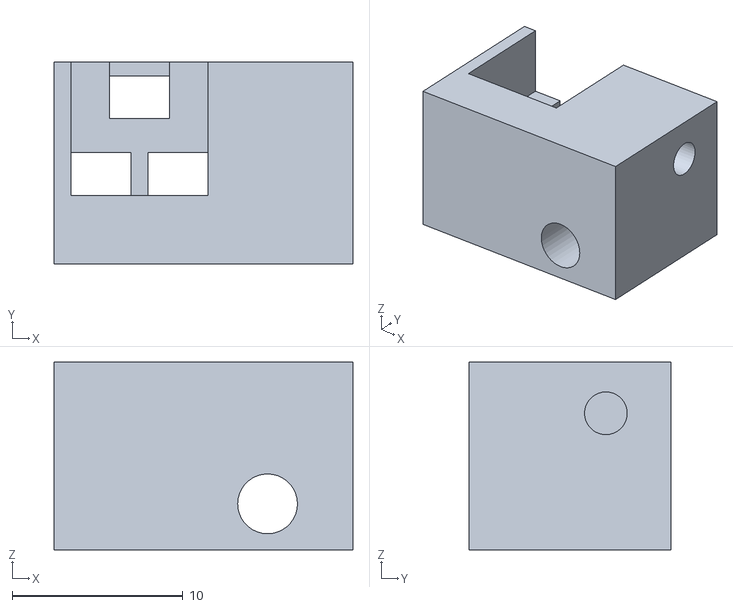
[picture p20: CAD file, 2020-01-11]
docs/images/prototype/mechanics/stl-files/00000022-Sensorhalter.STL
17.5 x 11.8 x 11.0

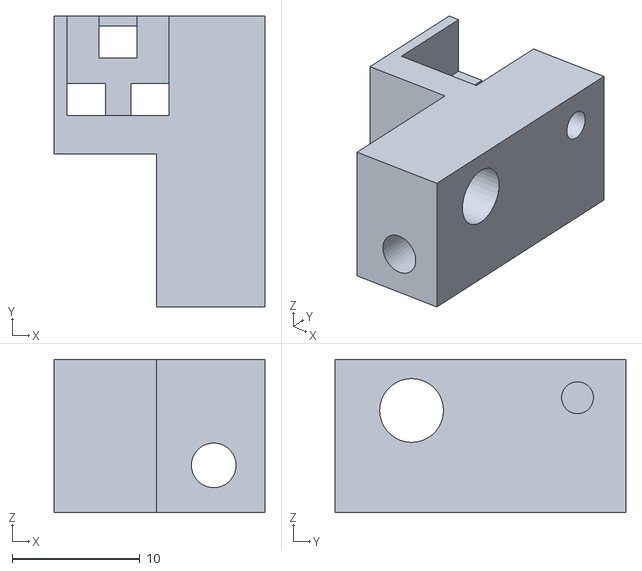
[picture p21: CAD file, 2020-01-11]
docs/images/prototype/mechanics/stl-files/00000026-Sensorhalter.STL
16.5 x 22.8 x 12.0

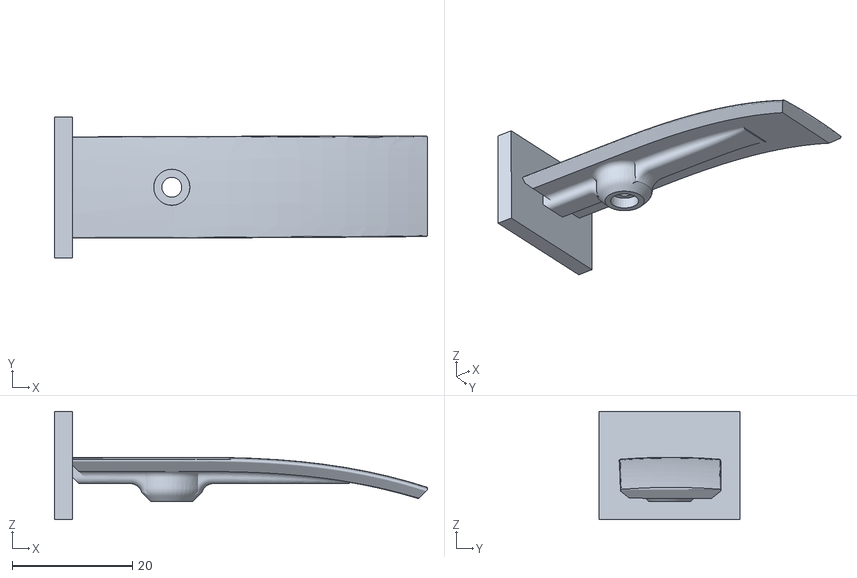
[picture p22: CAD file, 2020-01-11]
docs/images/prototype/mechanics/stl-files/00000011-Armlehne.STL
62.0 x 23.4 x 18.0

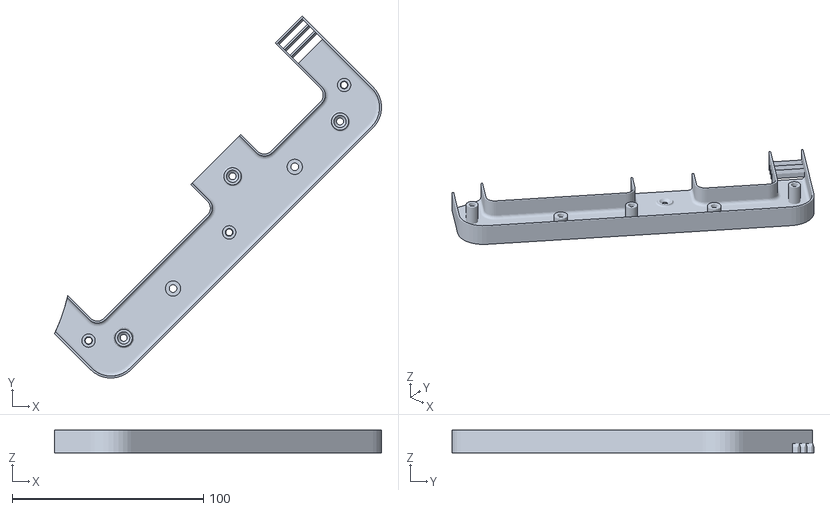
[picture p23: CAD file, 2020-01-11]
docs/images/prototype/mechanics/stl-files/00000054-Kabelkanal.STL
171.0 x 189.2 x 12.0

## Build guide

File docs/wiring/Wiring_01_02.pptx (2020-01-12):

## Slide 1

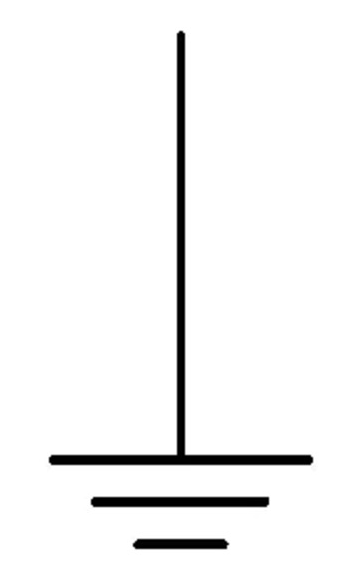
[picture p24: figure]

Poti 1

Motor 1

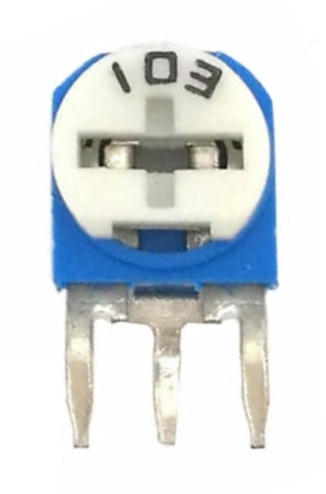
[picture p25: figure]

Poti 2

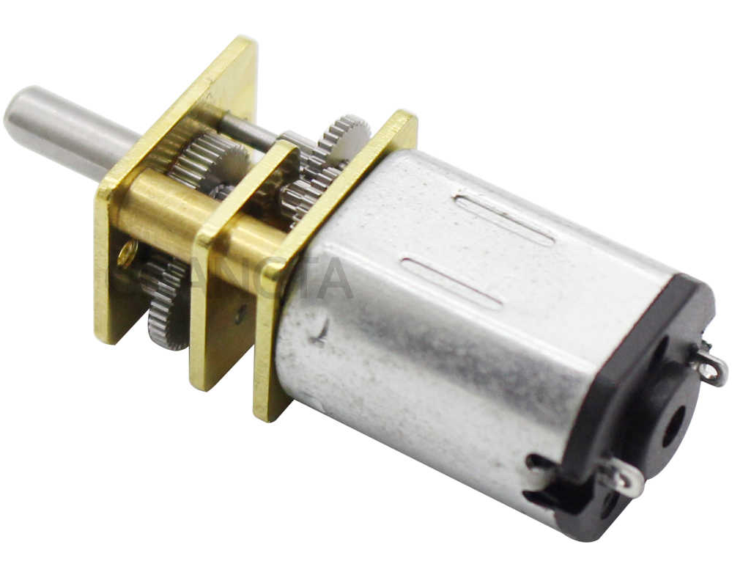
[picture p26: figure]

Motor 2

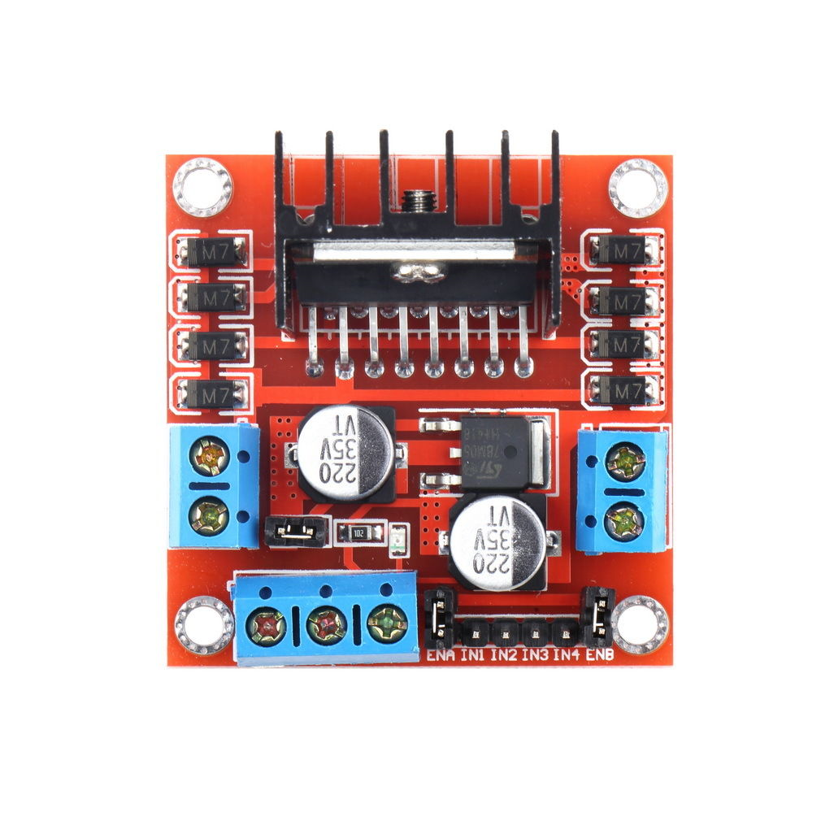
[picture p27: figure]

+6V

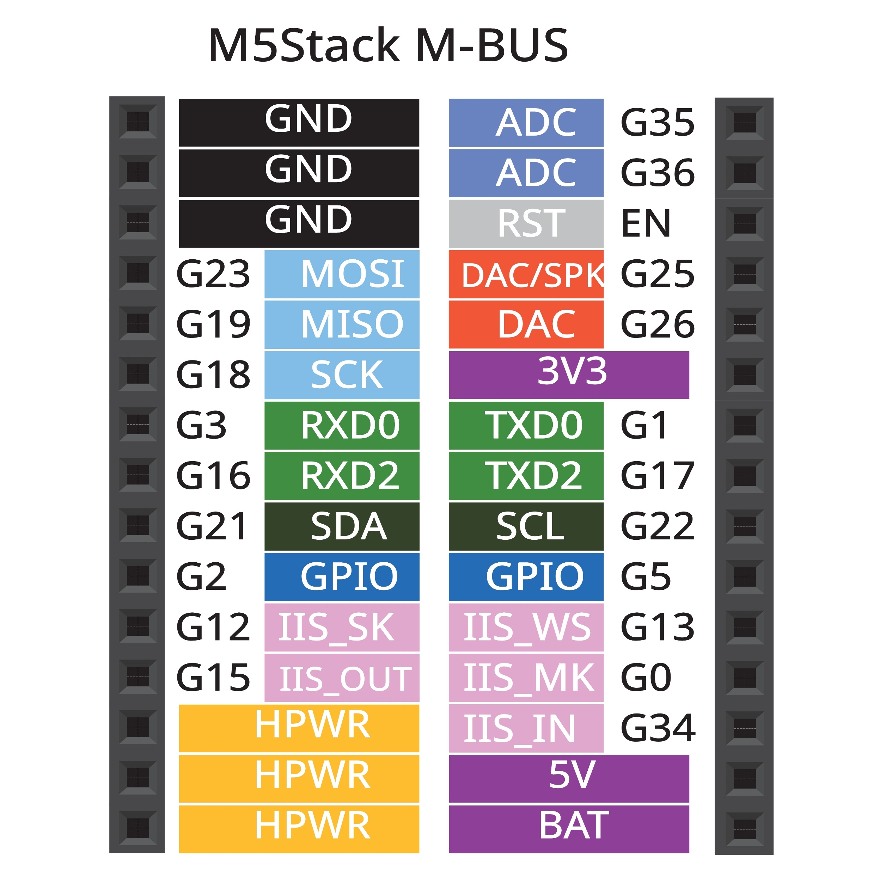
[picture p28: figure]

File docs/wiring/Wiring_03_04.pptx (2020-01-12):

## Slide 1


Poti 3

Motor 3


Poti 4


Motor 4


+6V


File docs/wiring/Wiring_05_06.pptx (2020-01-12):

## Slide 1


Poti 5

Motor 5


Poti 6


Motor 6


+6V


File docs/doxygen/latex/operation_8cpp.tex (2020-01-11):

\hypertarget{operation_8cpp}{}\doxysection{main/src/operation.cpp File Reference}
\label{operation_8cpp}\index{main/src/operation.cpp@{main/src/operation.cpp}}

Source code for the \mbox{\hyperlink{class_operation}{Operation}} class.  

{\ttfamily \#include \char`\"{}../include/operation.\+hpp\char`\"{}}\newline

\doxysubsection{Detailed Description}
Source code for the \mbox{\hyperlink{class_operation}{Operation}} class. 

\begin{DoxyAuthor}{Author}
Torsten Niemeier 

E-\/mail\+: \href{mailto:tniemeier1@fh-bielefeld.de}{\texttt{ tniemeier1@fh-\/bielefeld.\+de}} 
\end{DoxyAuthor}
\begin{DoxyVersion}{Version}
1.\+0 
\end{DoxyVersion}
\begin{DoxyDate}{Date}
2019/12/21
\end{DoxyDate}
\hypertarget{statemachine_8cpp_LICENSE}{}\doxysubsection{L\+I\+C\+E\+N\+SE}\label{statemachine_8cpp_LICENSE}
This program is free software; you can redistribute it and/or modify it under the terms of the G\+NU General Public License as published by the Free Software Foundation; either version 2 of the License, or (at your option) any later version.

This program is distributed in the hope that it will be useful, but W\+I\+T\+H\+O\+UT A\+NY W\+A\+R\+R\+A\+N\+TY; without even the implied warranty of M\+E\+R\+C\+H\+A\+N\+T\+A\+B\+I\+L\+I\+TY or F\+I\+T\+N\+E\+SS F\+OR A P\+A\+R\+T\+I\+C\+U\+L\+AR P\+U\+R\+P\+O\+SE. See the G\+NU General Public License for more details at \href{https://www.gnu.org/copyleft/gpl.html}{\texttt{ https\+://www.\+gnu.\+org/copyleft/gpl.\+html}}\hypertarget{statemachine_8cpp_DESCRIPTION}{}\doxysubsection{D\+E\+S\+C\+R\+I\+P\+T\+I\+ON}\label{statemachine_8cpp_DESCRIPTION}
The \mbox{\hyperlink{class_operation}{Operation}} class represents a function the \mbox{\hyperlink{class_smart_seat}{Smart\+Seat}} can perform.

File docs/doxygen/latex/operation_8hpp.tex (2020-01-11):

\hypertarget{operation_8hpp}{}\doxysection{main/include/operation.hpp File Reference}
\label{operation_8hpp}\index{main/include/operation.hpp@{main/include/operation.hpp}}

Header for the \mbox{\hyperlink{class_operation}{Operation}} class.  

{\ttfamily \#include \char`\"{}servo.\+hpp\char`\"{}}\newline
{\ttfamily \#include \char`\"{}light.\+hpp\char`\"{}}\newline
{\ttfamily \#include \char`\"{}heater.\+hpp\char`\"{}}\newline
\doxysubsection*{Classes}
\begin{DoxyCompactItemize}
\item 
class \mbox{\hyperlink{class_operation}{Operation}}
\end{DoxyCompactItemize}

\doxysubsection{Detailed Description}
Header for the \mbox{\hyperlink{class_operation}{Operation}} class. 

\begin{DoxyAuthor}{Author}
Torsten Niemeier 

E-\/mail\+: \href{mailto:tniemeier1@fh-bielefeld.de}{\texttt{ tniemeier1@fh-\/bielefeld.\+de}} 
\end{DoxyAuthor}
\begin{DoxyVersion}{Version}
1.\+0 
\end{DoxyVersion}
\begin{DoxyDate}{Date}
2020/01/03
\end{DoxyDate}
\hypertarget{statemachine_8cpp_LICENSE}{}\doxysubsection{L\+I\+C\+E\+N\+SE}\label{statemachine_8cpp_LICENSE}
This program is free software; you can redistribute it and/or modify it under the terms of the G\+NU General Public License as published by the Free Software Foundation; either version 2 of the License, or (at your option) any later version.

This program is distributed in the hope that it will be useful, but W\+I\+T\+H\+O\+UT A\+NY W\+A\+R\+R\+A\+N\+TY; without even the implied warranty of M\+E\+R\+C\+H\+A\+N\+T\+A\+B\+I\+L\+I\+TY or F\+I\+T\+N\+E\+SS F\+OR A P\+A\+R\+T\+I\+C\+U\+L\+AR P\+U\+R\+P\+O\+SE. See the G\+NU General Public License for more details at \href{https://www.gnu.org/copyleft/gpl.html}{\texttt{ https\+://www.\+gnu.\+org/copyleft/gpl.\+html}}\hypertarget{statemachine_8cpp_DESCRIPTION}{}\doxysubsection{D\+E\+S\+C\+R\+I\+P\+T\+I\+ON}\label{statemachine_8cpp_DESCRIPTION}
The \mbox{\hyperlink{class_operation}{Operation}} class represents a function the \mbox{\hyperlink{class_smart_seat}{Smart\+Seat}} can perform.

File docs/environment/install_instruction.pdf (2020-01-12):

Embedded Software
Praktikum SS2019
Prof. Dr. Dr.-Ing. Matthias König
M. Sc. Andrei Günter

# Praktikum 3

## Aufgabe 1

Richten Sie sich eine GNU-kompatible Umgebung ein und starten Sie mit der Programmierung des M5Stack Core.

a) Umgebung einrichten
Laden Sie sich die vorgefertigte Umgebung unter folgendem Link herunter: https://dl.espressif.com/dl/esp32_win32_msys2_environment_and_toolchain-20181001.zip

Entpacken Sie die heruntergeladene Datei und verschieben Sie den msys32 Ordner auf das Laufwerk, indem Windows installiert ist.

C:\msys32

b) ESP-IDF installieren
Installieren Sie die ESP-IDF in der Version 3.3 in Ihrer GNU-kompatiblen Umgebung. Öffnen Sie dazu eine mingw32 Konsole.

C:\msys32\mingw32.exe
Erstellen Sie nun einen Ordner, indem Sie die ESP-IDF installieren. Navigieren Sie in anschließend in den erstellten Ordner.

mkdir -p ~/esp && cd ~/esp
Klonen Sie abschließend das ESP-IDF mit folgendem Befehl.

git clone -b v3.3 --recursive https://github.com/espressif/esp-idf.git

Prof. Dr. Dr.-Ing. Matthias König
M. Sc. Andrei Günter
c) Umgebungsvariablen einrichten
Tipp: Ermöglichen Sie das Kopieren und Einfügen von Daten in die Konsole. Klicken Sie dazu mit einem Rechtsklick auf die Konsole und öffnen die Optionen. Im Tab „Keys“ können Sie die Checkbox „Ctrl+Shift+letter shortcuts“ aktivieren. Speichern Sie die Einstellung, um anschließend Daten mit „Strg+Shift+V“ einfügen zu können.

Erstellen Sie ein Skript für ihren Benutzer, welches eine Variable für das ESP-IDF einrichtet. Navigieren Sie dazu in folgendes Verzeichnis.

cd /etc/profile.d
Erstellen Sie nun das Skript:

vim export_idf_path.sh
Kopieren Sie folgende Zeile in das erstellte Skript und ändern S

ie den Teil „user-name“ in Ihren Benutzernamen und speichern Sie anschließend, indem Sie den Vim-Editor mit „:wq“ verlassen.

export IDF_PATH="C:/msys32/home/user-name/esp/esp-idf"
Schließen Sie die geöffnete Konsole und starten Sie eine neue Konsole, um das erstellte Skript zu testen. Sie sollten mit folgendem Befehl zum ESP-IDF Ordner navigieren können.

cd $IDF_PATH

d) Abhängigkeiten installieren
Installieren Sie die Python Abhängigkeiten, indem Sie den folgenden Befehl ausführen:

python -m pip install --user -r $IDF_PATH/requirements.txt

Prof. Dr. Dr.-Ing. Matthias König
M. Sc. Andrei Günter

## Aufgabe 2

Richten Sie eine Entwicklungsumgebung für den M5Stack ein.

a) M5Stack-IDF klonen
Navigieren Sie in Ihr zuvor erstelltes ESP-Verzeichnis:

cd ~/esp
Klonen Sie das M5Stack-IDF Repository und die entsprechenden Komponenten mit folgenden Befehlen:

git clone --recursive https://github.com/m5stack/M5Stack-IDF.git
Die Arduino-Komponente im Repository ist fehlerhaft, daher müssen Sie diese löschen und durch die aktuelle Version ersetzen:

cd ~/esp/M5Stack-IDF/components
rm -rf arduino
git clone https://github.com/espressif/arduino-esp32.git arduino cd arduino
git submodule update --init --recursive
b) M5Core programmieren
Schließen Sie Ihren M5Core an Ihren Rechner an und ermitteln Sie die entsprechende Schnittstelle, um den ESP32 Ihres M5Core mit einem Programm zu beschreiben. Konfigurieren Sie die Schnittstelle anschließend, indem Sie folgenden Befehl ausführen:

cd ~/esp/M5Stack-IDF
make menuconfig
Navigieren Sie im GUI zum entsprechenden Menüpunkt, um die Schnittstelle zu konfigurieren (Bspw. COM8).

Serial flashen config → Default serial port → COM8
Navigieren Sie im GUI anschließend zu folgendem Menüpunkt und aktivieren Sie mit der Taste „y“ die Cipher Suite.

Component config → mBedTLS → TLS Key Exchange Methods

→ Enable pre-shared-key ciphersuites
Speichern und verlassen Sie die Konfiguration. Laden Sie anschließend das Programm auf den M5Core. Sie sollten „Hello world“ als Ausgabe auf dem Display des M5 Core sehen.

make flash

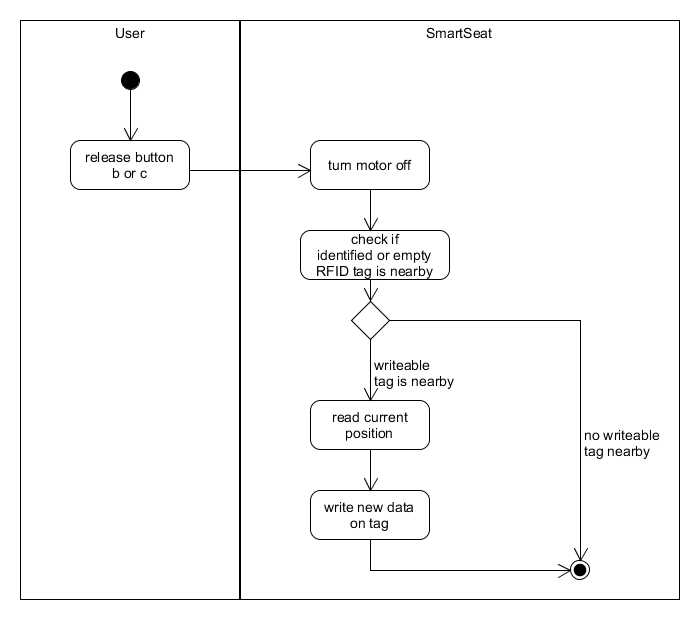
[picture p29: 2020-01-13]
docs/diagrams/activity/activity_manual_adjust_release_key.png

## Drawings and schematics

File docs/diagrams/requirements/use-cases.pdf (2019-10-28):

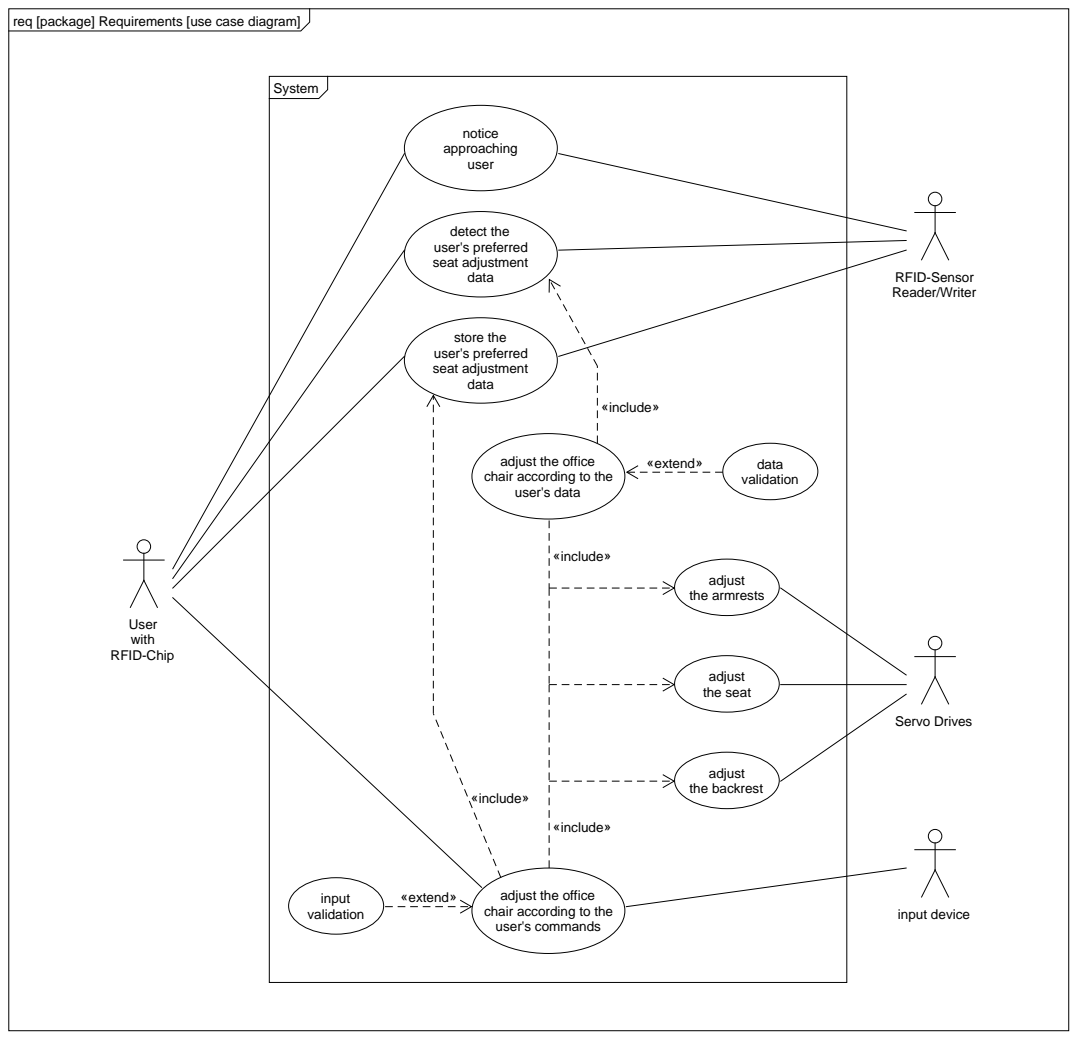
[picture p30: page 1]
input validation; data validation; input device; store the user's preferred seat adjustment data; Servo Drives; adjust the armrests; adjust the backrest; adjust the seat; RFID-Sensor Reader/Writer; detect the user's preferred seat adjustment data; notice approaching user; System; User with RFID-Chip; «extend»; «include»

req [package] Requirements [use case diagram]

adjust the office
chair according to the
user's data

user's commands

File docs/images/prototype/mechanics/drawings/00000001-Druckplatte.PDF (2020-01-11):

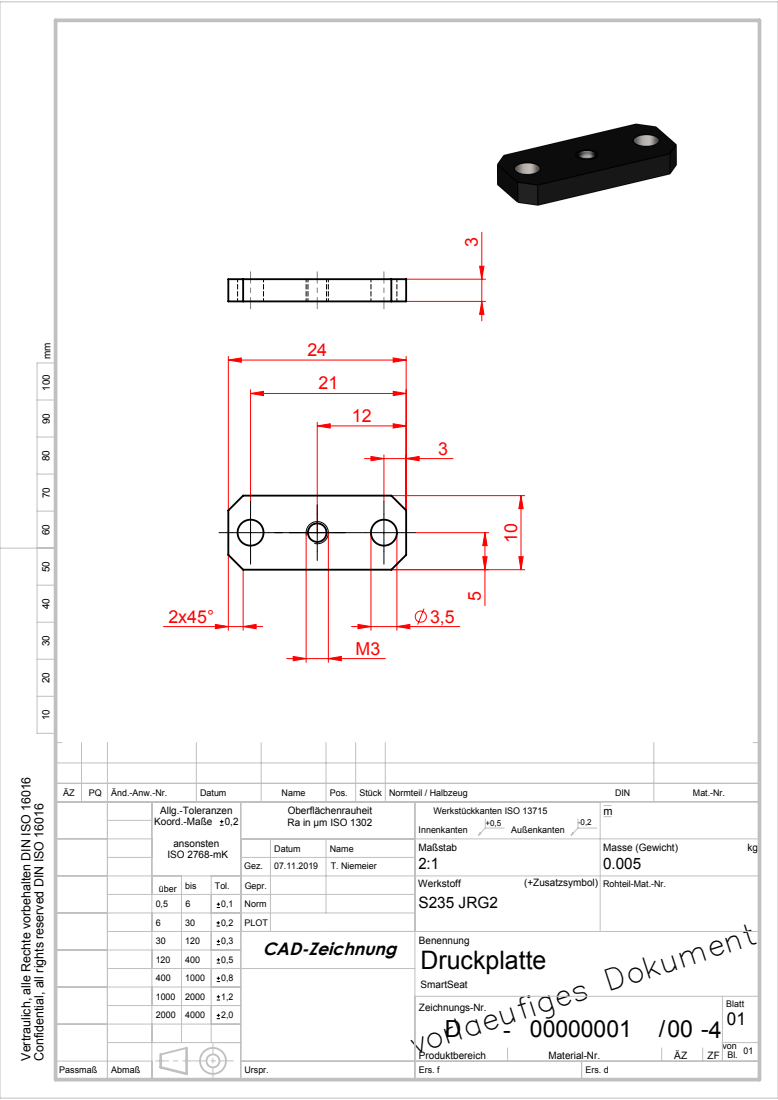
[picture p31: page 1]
vorlaeufiges Dokument; 07.11.2019 T. Niemeier; S235 JRG2; ÄZ PQ Änd.-Anw.-Nr.; Datum; Name; Pos. Stück Normteil / Halbzeug; DIN; Mat.-Nr.; Masse (Gewicht); Werkstückkanten ISO 13715; Passmaß Abmaß; Urspr.; Ers. f; Ers. d; bis; Tol. über; Koord.-Maße 0,2; ISO 2768-mK

Confidential, all rights reserved DIN ISO 16016 10 20 30 40 50 60 70 80 90 100 mm

Vertraulich, alle Rechte vorbehalten DIN ISO 16016

Oberflächenrauheit
Ra in µm ISO 1302

Rohteil-Mat.-Nr.

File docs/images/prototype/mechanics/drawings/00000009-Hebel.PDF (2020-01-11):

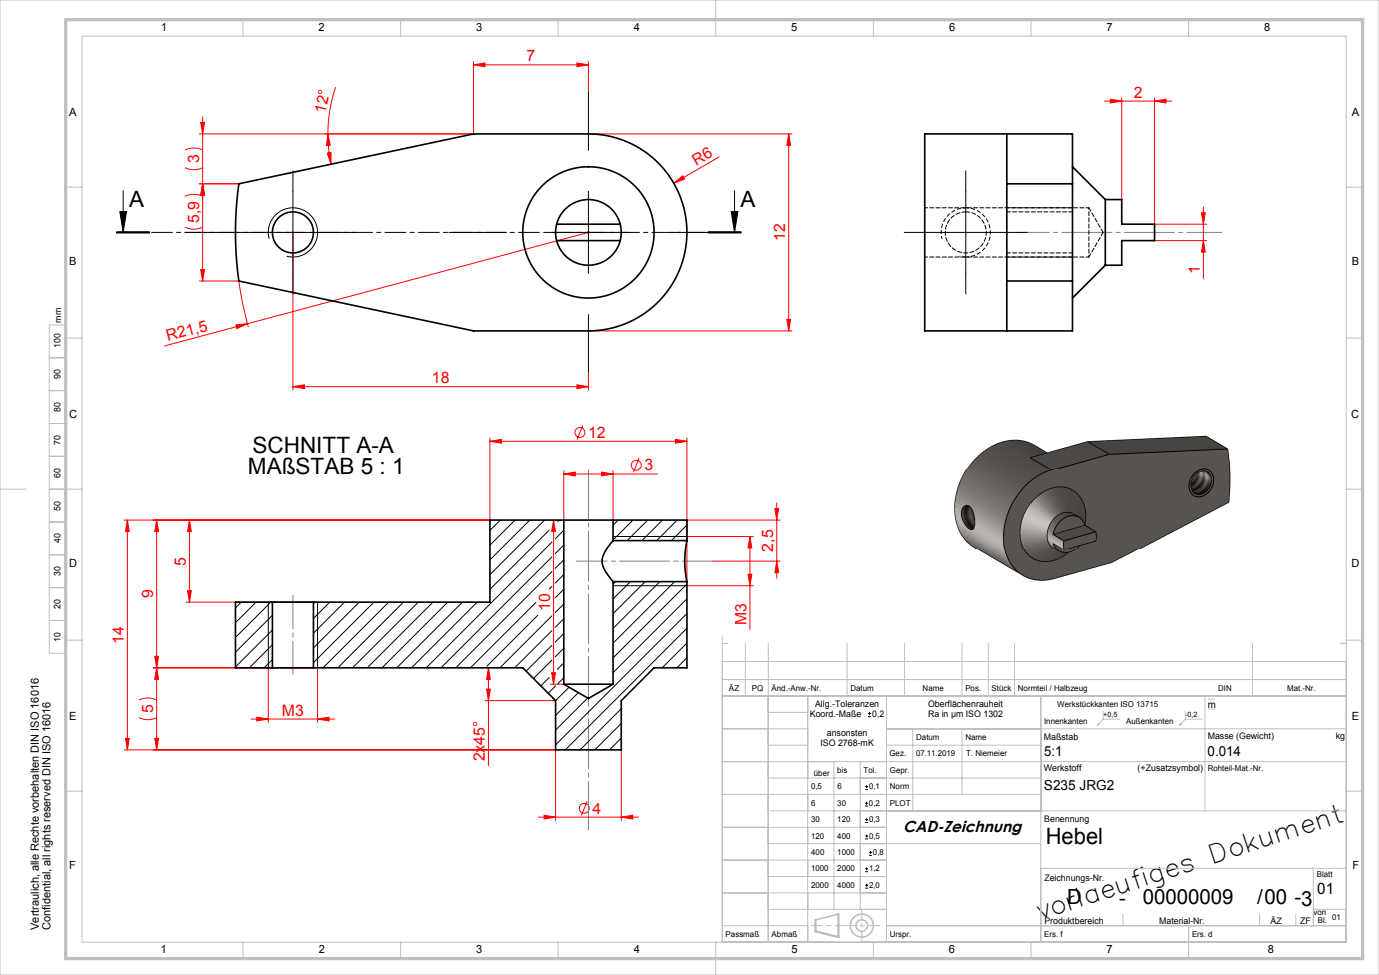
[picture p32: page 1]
SCHNITT A-A MAßSTAB 5 : 1; vorlaeufiges Dokument D - /00 -; 07.11.2019 T. Niemeier; S235 JRG2; ÄZ PQ Änd.-Anw.-Nr.; Datum; Name; Pos. Stück Normteil / Halbzeug; DIN; Mat.-Nr.; Masse (Gewicht); Werkstückkanten ISO 13715; Passmaß Abmaß; Urspr.; Ers. f; Ers. d; bis; Tol. über; Koord.-Maße 0,2; ISO 2768-mK; CAD-Zeichnung Hebel

Vertraulich, alle Rechte vorbehalten DIN ISO 16016

Oberflächenrauheit
Ra in µm ISO 1302

Confidential, all rights reserved DIN ISO 16016

Rohteil-Mat.-Nr.

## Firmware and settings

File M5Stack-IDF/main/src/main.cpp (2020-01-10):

/**
 * @file main.cpp
 * @brief The main function of the SmartSeat 
 *
 * @author	Torsten Niemeier
 * @author	E-mail: <tniemeier1@fh-bielefeld.de>
 * @version 1.0
 * @date 2019/12/21
 *
 * @section LICENSE
 *
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
 * @section DESCRIPTION
 *
 * The main function ist the global function for the SmartSeat,
 * which is the designated start of the program.
 */

#include "../lib/M5Stack_new.h"
#include "../include/smartseat.hpp"

#if CONFIG_FREERTOS_UNICORE
#define ARDUINO_RUNNING_CORE 0
#else
#define ARDUINO_RUNNING_CORE 1
#endif


SmartSeat smartseat("The incredible Seat");


// The setup routine runs once when M5Stack starts up
void setup(){

    // M5.begin with LCDEnable, SDEnable, SerialEnable, I2CEnable
	// The begin function is located in the library "M5Stack_new".
	// It is necessary, to start the M5 without enabling Serial, which the 'old' component "M5Stack" doesn't allow.  	
	M5.begin(true, false, false, true); 

	// Serial may not be started if the SmartSeat shall operate normally.
	// Erase the outcomment of the line for debug purposes, but don't give electrical power to the motor drivers then.
	// Serial.begin(115200);

	// begin Wire library for I2C-RFID-functionality
	Wire.begin();
	
	// initialize the SmartSeat
	smartseat.init();
}


void loop() {
	M5.update();
	if(M5.BtnA.wasPressed()){
        smartseat.getStateMachine()->eventButtonA();
    } 
    if(M5.BtnB.read()){
        smartseat.getStateMachine()->eventButtonB();
    }
    if(M5.BtnC.read()){
        smartseat.getStateMachine()->eventButtonC();
    }
    if(smartseat.getRfidUnit()->detectCard()){
        smartseat.getStateMachine()->eventRfid();
    }
}


// The arduino task
void loopTask(void *pvParameters)
{
    setup();
    for(;;) {
        micros(); //update overflow
        loop();
    }
}

extern "C" void app_main()
{
    initArduino();
    xTaskCreatePinnedToCore(loopTask, "loopTask", 8192, NULL, 1, NULL, ARDUINO_RUNNING_CORE);
}

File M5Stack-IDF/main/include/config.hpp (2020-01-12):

/**
 * @file config.hpp
 * @brief Header for a SmartSeat's general configuration values 
 *
 * @author	Torsten Niemeier
 * @author	E-mail: <tniemeier1@fh-bielefeld.de>
 * @version 1.0
 * @date 2019/12/30
 *
 * @section LICENSE
 *
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
 * @section DESCRIPTION
 *
 * config.hpp includes definitions and enums used by a SmartSeat
 */

#ifndef CONFIG_HPP
#define CONFIG_HPP

#ifdef __cplusplus
extern "C" {
#endif

// motor 01
#define MOTOR_01_PIN_01 2
#define MOTOR_01_PIN_02 15

// motor 02
#define MOTOR_02_PIN_01 3
#define MOTOR_02_PIN_02 1

// motor 03
#define MOTOR_03_PIN_01 5
#define MOTOR_03_PIN_02 0

// motor 04
#define MOTOR_04_PIN_01 2
#define MOTOR_04_PIN_02 15

// motor 05
#define MOTOR_05_PIN_01 3
#define MOTOR_05_PIN_02 1

// motor 06
#define MOTOR_06_PIN_01 0
#define MOTOR_06_PIN_02 5

// potentiometer 01
#define POTI_01_PIN 26
#define POTI_01_MIN_VOLTAGE 1000
#define POTI_01_MAX_VOLTAGE 3350

// potentiometer 02
#define POTI_02_PIN 25
#define POTI_02_MIN_VOLTAGE 1270
#define POTI_02_MAX_VOLTAGE 3150

// potentiometer 03
#define POTI_03_PIN 13
#define POTI_03_MIN_VOLTAGE 1060
#define POTI_03_MAX_VOLTAGE 1120

// potentiometer 04
#define POTI_04_PIN 12
#define POTI_04_MIN_VOLTAGE 100
#define POTI_04_MAX_VOLTAGE 2800

// potentiometer 05
#define POTI_05_PIN 35
#define POTI_05_MIN_VOLTAGE 600
#define POTI_05_MAX_VOLTAGE 2500

// potentiometer 06
#define POTI_06_PIN 36
#define POTI_06_MIN_VOLTAGE 200
#define POTI_06_MAX_VOLTAGE 1300

// servo
#define SERVO_TIMEOUT 3000

// pwm 01
#define PWM_01_CHANNEL 0
#define PWM_01_FREQUENCY 30000
#define PWM_01_RESOLUTION 8
#define PWM_01_MIN_CYCLE 160
#define PWM_01_MAX_CYCLE 255
#define PWM_01_PIN 16

// pwm 02
#define PWM_02_CHANNEL 1
#define PWM_02_FREQUENCY 30000
#define PWM_02_RESOLUTION 8
#define PWM_02_MIN_CYCLE 160
#define PWM_02_MAX_CYCLE 255
#define PWM_02_PIN 17

// lcd
#define LCD_DISPLAY_WIDTH 320
#define LCD_DISPLAY_HEIGHT 240
#define LCD_DISPLAY_BRIGHTNESS 200

// rfid
#define RFID_I2C_ADDRESS 0x28
#define RFID_CHECK_INTERVAL 200 //milliseconds
#define RFID_NUMBER_OF_BLOCKS 64
#define RFID_BYTES_PER_BLOCK 16
const int RFID_USED_BLOCKS[21] = {4, 8, 9, 12, 13, 16, 17, 20, 21, 24, 25, 28, 29, 32, 33, 36, 37, 40, 41, 44, 45};
#define RFID_IDENTIFY_BLOCK 4
const int RFID_NAME_BLOCKS[10] = {8, 12, 16, 20, 24, 28, 32, 36, 40, 44};
#define RFID_IDENTIFY_NAME "SmartSeat"
enum CardState {empty, identified, unknown}; 

// operation specific
struct Target
{
    int operationIndex;
    float percentageGoal;
	int valueBlockOnPICC;
};


#ifdef __cplusplus
}
#endif

#endif 

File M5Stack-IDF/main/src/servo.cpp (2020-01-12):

/**
 * @file servo.cpp
 * @brief Source code for the Servo class
 *
 * @author	Torsten Niemeier
 * @author	E-mail: <tniemeier1@fh-bielefeld.de>
 * @version 1.0
 * @date 2019/12/21
 *
 * @section LICENSE
 *
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
 * @section DESCRIPTION
 *
 * The Servo class represents a combination of one motor and one potentiometer.
 */

#include "../include/servo.hpp"



/**
 * @brief Constructor
 * @brief The function creates a Servo object.
 *
 * @param motor - a pointer to the Servo's assigned Motor class instance
 * @param potentiometer - a pointer to the Servo's assigned Potentiometer class instance
 * @param changeMotDir - a bool value that defines if the Motor direction shall be inverted
 * @param changePotiDir - a bool value that defines if the Potentiometer direction shall be inverted
 * @return nothing
 */
Servo::Servo(Motor* motor, Potentiometer* potentiometer, bool changeMotDir, bool changePotiDir, float percSpeedForward, float percSpeedBackward)
	: servoMotor(motor), servoPotentiometer(potentiometer), changeMotorDirection(changeMotDir), changePotiDirection(changePotiDir), percentageSpeedForward(percSpeedForward), percentageSpeedBackward(percSpeedBackward)
{
}


/**
 * @brief Destructor
 * @brief The function destroys a Servo object.
 *
 * @return nothing 
 */
Servo::~Servo()
{
	delete servoMotor;
	delete servoPotentiometer;
}


/**
 * @brief The function gets the Servo's potentiometer.
 *
 * @return Potentiometer* - a pointer to the Servo's assigned Potentiometer class instance
 */
Potentiometer* Servo::getPotentiometer(){
	return servoPotentiometer;
}


/**
 * @brief The function gets the Servo's Motor.
 *
 * @return Motor* - a pointer to the Servo's assigned Motor class instance
 */
Motor* Servo::getMotor(){
	return servoMotor;
}


/**
 * @brief The function gets the Servo's Potentiometer voltage.
 *
 * @return uint16_t - the value represents the Potentiometer's current voltage level (0-4096)
 */
uint16_t Servo::getVoltage(){
	return servoPotentiometer->getVoltage();
}


/**
 * @brief The function gets if the Servo's Potentiometer direction is flipped.
 *
 * @return bool - the return value is true if the Potentiometer direction is flipped, false otherwise.
 */
bool Servo::getChangePotiDirection(){
	return changePotiDirection;
}


/**
 * @brief The function gets the Servo's assigned percentaged speed in forward direction.
 *
 * @return float - the return value is the Servo's assigned percentaged (0.0 - 100.0) forward speed.
 */
float Servo::getPercentageSpeedForward(){
	return percentageSpeedForward;
}


/**
 * @brief The function gets the Servo's assigned percentaged speed in backward direction.
 *
 * @return float - the return value is the Servo's assigned percentaged (0.0 - 100.0) backward speed.
 */
float Servo::getPercentageSpeedBackward(){
	return percentageSpeedBackward;
}


/**
 * @brief The function sets the Servo's Motor to move forward.
 *
 * @return nothing
 */
void Servo::moveForward(){
	if(changeMotorDirection){
		servoMotor->moveBackward();
	} else {
		servoMotor->moveForward();
	}
}


/**
 * @brief The function sets the Servo's Motor to move backward.
 *
 * @return nothing
 */
void Servo::moveBackward(){
	if(changeMotorDirection){
		servoMotor->moveForward();
	} else {
		servoMotor->moveBackward();
	}
}


/**
 * @brief The function sets the Servo's Motor to stop.
 *
 * @return 	nothing
 */
void Servo::stop(){
	servoMotor->stop();
}


/**
 * @brief The function get the current percentage position of the Servo.
 *
 * @return float - the return value represents the current percentage position of the Servo.
 * If the Servo's Potentiometer is initialized irregular the function returns -100.0.
 */
float Servo::getPercentagePosition(){
	float currentVoltage = getVoltage();
	float minVoltage = servoPotentiometer->getMinVoltageLevel();
	float maxVoltage = servoPotentiometer->getMaxVoltageLevel();
	float percentage;

	if (maxVoltage - minVoltage > 0){
		if(getChangePotiDirection()){
			percentage = 100 - (currentVoltage - minVoltage) / (maxVoltage - minVoltage) * 100;
		} else {
			percentage = (currentVoltage - minVoltage) / (maxVoltage - minVoltage) * 100;
		}
		if (percentage > 100.0) {
			percentage = 100.0;
		}
		if (percentage < 0.0) {
			percentage = 0.0;
		}
		return percentage;
	} else {
		return -100.0;
	}
}


/**
 * @brief The function moves the Servo to a given position target.
 *
 * @param target - float value that represents the percentage amount of voltage level at the Servo's Potentiometer that shall be reached
 * @return bool - the return value is true if the voltage target could be reached, false otherwise
 */
bool Servo::moveToTarget(float target, float startSpeed){
	unsigned long startTime = millis();
	float currentPosition = getPercentagePosition();
	bool stopped;
	
	Serial.printf("Servo's current position is %.1f%%\n", currentPosition);
	Serial.printf("Servo tries to reach target %.1f%%\n", target);

	// set speeder
	getMotor()->getSpeeder()->turnOn(startSpeed);

	// drive to target
	if (currentPosition > target){
		stopped = false;
		while (currentPosition > target && currentPosition > 0 && millis() < startTime + SERVO_TIMEOUT && !stopped){
			currentPosition = getPercentagePosition();
			if(currentPosition > target){
				moveBackward();
			} else {
				stop();
				stopped = true;
			}
			if (abs(currentPosition - target) < 1.0){
				getMotor()->getSpeeder()->turnOn(startSpeed * 0.2);
			} else if (abs(currentPosition - target) < 5.0){
				getMotor()->getSpeeder()->turnOn(startSpeed * 0.8);
			}
		}
		stop();
	} else {
		stopped = false;
		while (currentPosition < target && currentPosition < 100 && millis() < startTime + SERVO_TIMEOUT && !stopped){
			currentPosition = getPercentagePosition();
			if(currentPosition < target){
				moveForward();
			} else {
				stop();
				stopped = true;
			}
			if (abs(currentPosition - target) < 1.0){
				getMotor()->getSpeeder()->turnOn(startSpeed * 0.2);
			} else if (abs(currentPosition - target) < 5.0){
				getMotor()->getSpeeder()->turnOn(startSpeed * 0.8);
			}
		}
		stop();
	}
	stop();
	getMotor()->getSpeeder()->turnOff();

	// check result
	if (millis() < startTime + SERVO_TIMEOUT) {
		return true;
	} else {
		return false;
	}
}

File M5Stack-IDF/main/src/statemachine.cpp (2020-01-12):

/**
 * @file statemachine.cpp
 * @brief Source code for the StateMachine class
 *
 * @author	Torsten Niemeier
 * @author	E-mail: <tniemeier1@fh-bielefeld.de>
 * @version 1.0
 * @date 2019/12/21
 *
 * @section LICENSE
 *
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
 * @section DESCRIPTION
 *
 * The StateMachine class represents a state machine for the operations
 * of the SmartSeat.
 */

#include "../include/statemachine.hpp"
#include <M5Display.h>

bool serviceMode = false;

/**
 * @brief Constructor
 * @brief The function creates a StateMachine object.
 *
 * @return nothing
 */
StateMachine::StateMachine()
{
}


/**
 * @brief Destructor
 * @brief The function destroys a StateMachine object.
 *
 * @return 	nothing 
 */
StateMachine::~StateMachine()
{
}


/**
 * @brief The function writes new operation data to the PICC.
 *
 * @return nothing
 */
void StateMachine::writeDataToPICC(float currentPosition)
{
	std::vector<Target> piccTargets;
	Target newTarget;
	bool dataWritten;
	std::vector<byte> byteBlock;
	int sum;

	Serial.printf("StateMachine::writeDataToPICC\n");

	// write new settings if PICC is present
	dataWritten = false;
	if (rfidUnit->getCardPresence()){
		Serial.printf("Card is present.\n");
		if (rfidUnit->getCardState() == identified) {
			Serial.printf("Card is identified.\n");
			// search, if current operation has already a value
			piccTargets = rfidUnit->getTargets();
			for (int i = 0; i < piccTargets.size(); i++){
				if (piccTargets.at(i).operationIndex == currentState) {
					// write data on PICC
					dataWritten = rfidUnit->writeData(piccTargets.at(i).valueBlockOnPICC, String(currentPosition));
					if (dataWritten) {
						piccTargets.at(i).percentageGoal = currentPosition;
					}
				}
			}
			// if current operation has no value on the PICC, take next empty block
			if (!dataWritten) {
				for (int i = 0; i < (sizeof(RFID_NAME_BLOCKS) / sizeof(*RFID_NAME_BLOCKS)); i++){
					if (!dataWritten) {
						byteBlock = rfidUnit->readBlockArray(RFID_NAME_BLOCKS[i]);
						sum = 0;
						for(int j = 0 ; j < RFID_BYTES_PER_BLOCK; j++){
							sum += byteBlock.at(j);
						}
						if (sum == 0) {
							dataWritten = rfidUnit->writeData(RFID_NAME_BLOCKS[i], operations.at(currentState)->getOperationName());
							dataWritten = rfidUnit->writeData(RFID_NAME_BLOCKS[i] + 1, String(currentPosition));
							if (dataWritten) {
								newTarget.operationIndex = currentState;
								newTarget.percentageGoal = currentPosition;
								newTarget.valueBlockOnPICC = RFID_NAME_BLOCKS[i] + 1;
								rfidUnit->addTarget(newTarget);
							}
						}
					}
				}
			}			
		}
		if (rfidUnit->getCardState() == empty) {
			Serial.printf("Card is empty.\n");
			// write identy String on PICC
			rfidUnit->writeData(RFID_IDENTIFY_BLOCK, RFID_IDENTIFY_NAME);
			// write new data on PICC
			dataWritten = rfidUnit->writeData(RFID_NAME_BLOCKS[0], operations.at(currentState)->getOperationName());
			dataWritten = rfidUnit->writeData(RFID_NAME_BLOCKS[0] + 1, String(currentPosition));
			if (dataWritten) {
				newTarget.operationIndex = currentState;
				newTarget.percentageGoal = currentPosition;
				newTarget.valueBlockOnPICC = RFID_NAME_BLOCKS[0] + 1;
				rfidUnit->addTarget(newTarget);
			}
		}
	}
}


/**
 * @brief The function reacts on the event: 'Button A is pressed'.
 *
 * @return nothing
 */
void StateMachine::eventButtonA()
{
	float currentPosition;

    currentState ++;
	if (currentState >= numberOfStates) {
		currentState = 0;
	} 

	// serial info
	Serial.printf("Operation Modus has changed: current state is %i\n", currentState);
	Serial.print("operationName: ");
	Serial.println(operations.at(currentState)->getOperationName());
	
	lcdDisplay->displayImageArray(operations.at(currentState)->getImageArray());

	if (operations.at(currentState)->getOperationType() == "servo"){
		currentPosition = operations.at(currentState)->getOperationServo()->getPercentagePosition();
		lcdDisplay->displayPercentage(currentPosition);
		if (serviceMode) {lcdDisplay->displayVoltage(operations.at(currentState)->getOperationServo()->getVoltage());}
	
		// turn off all speeders
		for(std::size_t i = 0; i < speeders.size(); i++) {
			speeders.at(i)->turnOff();
		} 
	
	}
}


/**
 * @brief The function reacts on the event: 'Button B is pressed'.
 *
 * @return nothing
 */
void StateMachine::eventButtonB()
{
	float specificSpeed;
	float currentPosition;
	
	// serial info
	Serial.printf("Button B was pressed.\n");
	Serial.printf("currentState = %i\n", currentState);
	Serial.printf("operationName = '%s'\n", operations.at(currentState)->getOperationName().c_str());

	if (operations.at(currentState)->getOperationType() == "servo"){
		// turn on spezific speeder
		specificSpeed = operations.at(currentState)->getOperationServo()->getPercentageSpeedBackward();
		operations.at(currentState)->getOperationServo()->getMotor()->getSpeeder()->turnOn(specificSpeed);
		// move servo while button is pressed
		while(M5.BtnB.read()){
			if (serviceMode) {lcdDisplay->displayVoltage(operations.at(currentState)->getOperationServo()->getVoltage());}
			currentPosition = operations.at(currentState)->getOperationServo()->getPercentagePosition();
			lcdDisplay->displayPercentage(currentPosition);
			if(currentPosition > 0){
				operations.at(currentState)->getOperationServo()->moveBackward();
			} else {
				operations.at(currentState)->getOperationServo()->stop();
			}			
		}
		// stop servo, update current position
		operations.at(currentState)->getOperationServo()->stop();
		if (serviceMode) {lcdDisplay->displayVoltage(operations.at(currentState)->getOperationServo()->getVoltage());}
		currentPosition = operations.at(currentState)->getOperationServo()->getPercentagePosition();
		lcdDisplay->displayPercentage(currentPosition);
		writeDataToPICC(currentPosition);
	}
}
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

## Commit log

2020-01-09 upload first working prototype M5Stack-IDF
2020-01-09 upload first working prototype code
2020-01-09 finally, first working prototype code
2020-01-09 initial upload first working prototype code
    [partitions_singleapp_custom.csv]
2020-01-09 repair upload
    [partitions_singleapp_custom.csv]
2020-01-11 mechanical models, drawings and stl-files added
    [00000011-Armlehne.STL, 00000021-Sensorhalter.STL, 00000022-Sensorhalter.STL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]
2020-01-11 bom images added
2020-01-12 wiring diagrams added
2020-01-12 reorganize environment section
    [partitions_singleapp_custom.csv]
